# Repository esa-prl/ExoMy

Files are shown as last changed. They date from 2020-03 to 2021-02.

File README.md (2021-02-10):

# ExoMy - Documentation Repository
This repository contains all the files of the documentation of ExoMy. Click on [*Releases*](https://github.com/esa-prl/ExoMy/releases) and download the files of the latest release.
The release file contains the 3D files (STL, SLDPRT & STEP), circuit diagrams, part lists, etc. to build your own ExoMy.
The building process and the files are explained further in the [wiki](https://github.com/esa-prl/ExoMy/wiki).

# ExoMy Project Structure
Overview of other parts of the ExoMy project.

### [Wiki](https://github.com/esa-prl/ExoMy/wiki)
The [wiki](https://github.com/esa-prl/ExoMy/wiki) contains step by step instructions on how the 3D-printed rover ExoMy can be built, controlled and customized.  

<!-- ### [Documentation Repository](https://github.com/esa-prl/ExoMy)
This repository contains all the files of the documentation of ExoMy. Just click on [*Releases*](https://github.com/esa-prl/ExoMy/releases) and download the files of the latest release. They are explained further in the [wiki](https://github.com/esa-prl/ExoMy/wiki). -->

### [Website](https://esa-prl.github.io/ExoMy/)
There is a website about ExoMy. It does not help you build it, but is still nice to look at.

### [Software Repository](https://github.com/esa-prl/ExoMy_Software)
This repository contains the software to run Exomy. The [wiki](https://github.com/esa-prl/ExoMy/wiki) explains you how to use it.

### Social Media
<!-- Add icon library -->
<link rel="stylesheet" href="https://use.fontawesome.com/releases/v5.13.1/css/all.css">

<!-- Add font awesome icons -->
<p>
    
    <a href="https://discord.gg/gZk62gg"> Join the Community!</a>  
</p>
<p>
    
    <a href="https://twitter.com/exomy_rover"> @ExoMy_Rover</a> 
</p>
<p>
    
    <a href="https://www.instagram.com/exomy_rover/"> @ExoMy_Rover</a>
</p>

ExoMy image

### Publications

If you use this work in an academic context, please cite the following publication:

* M. Voellmy and M. Ehrhardt: **ExoMy: A Low Cost 3D Printed Rover**. International Symposium on Artificial Intelligence, Robotics and Automation in Space (i-SAIRAS), 2020. ([PDF](https://www.researchgate.net/publication/344874558_ExoMy_A_Low_Cost_3D_Printed_Rover))

        @inproceedings{inproceedings,
        author = {Voellmy, Miro and Ehrhardt, Maximilian},
        year = {2020},
        month = {10},
        pages = {},
        title = {ExoMy: A Low Cost 3D Printed Rover}
        }

### Acknowledgements

ExoMy was developed in the Planetary Robotics Laboratory of the European Space Agency.

The current team developing and maintaining ExoMy consists of Maximilian Ehrhardt, Miro Voellmy and Lorenzo Cervantes.

ExoMy Generations

We thank Shanker Ganesh Krishanmoorthy and Levin Gerdes for the development of the initial prototype, David Honess and Elsa María Sánchez for participating in the documented assembly, Tim Wiese and Mattia Haas for their inputs and contributions to the mechanical design, and finally Martin Azkarate, Martin Zwick and Gianfranco Visentin for enabling and continuously supporting the project.

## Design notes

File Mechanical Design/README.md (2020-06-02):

# CAD Design Guidelines

ExoMy was designed using SolidWorks 2018. No additional toolboxes were used.

## Folder Structure
Assemblies and 3D printed parts are to be stored in the main folder.

```
- Mechanical Design
Assemblies and parts go here.
-- Cables
-- Drawings
-- Fasteners
-- Purchased Parts
-- Templates
```

## Part Naming
The file naming convention is as follows:

**Assemblies**

*`Axx_Name_with_underscore.SLDASM`*

**3D-Printed Parts**

*`Pxx_Name_with_underscores.SLDPRT`*

Replace xx with a new two-digit part-/assemby-number.

**Always** use a new number for a new part/assembly. Don't try to fill in the gaps that occur if old parts are deleted.

## Configurations
Configurations are used to generate variations of parts (rear/side bogie, left/right wheelbracket, various hats.). They are also used to create drawings and bill of materials. All *`AI_*`* & *`MI_*`* drawings are linked to a similarly named configuration of the main assembly or a subassembly. This allows the generation of a bill of materials, which can then be exported to Excel.

The naming should be kept consist to simplify the referencing in the wiki in case of new releases.

## Exporting and Releases
Refer to the [wikipage](https://github.com/esa-prl/ExoMy/wiki/Release-Procedure#solidworks).

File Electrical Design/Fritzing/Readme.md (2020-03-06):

# ExoMy Fritzing project

This folder contains everything you need to open the ExoMy electronics as a Fritzing project.

## Exomy.fzz
Is the main Project file.

## Exomy_bin.fzbz
The library file that contains all the parts used for the project.

## parts
All the Fritzing pars used in the project. The files are normal archives and can be opened with any archive program, to access the underlying svg files.
## exports
The exported views of breadboard and schematic as pdf and svg file format.

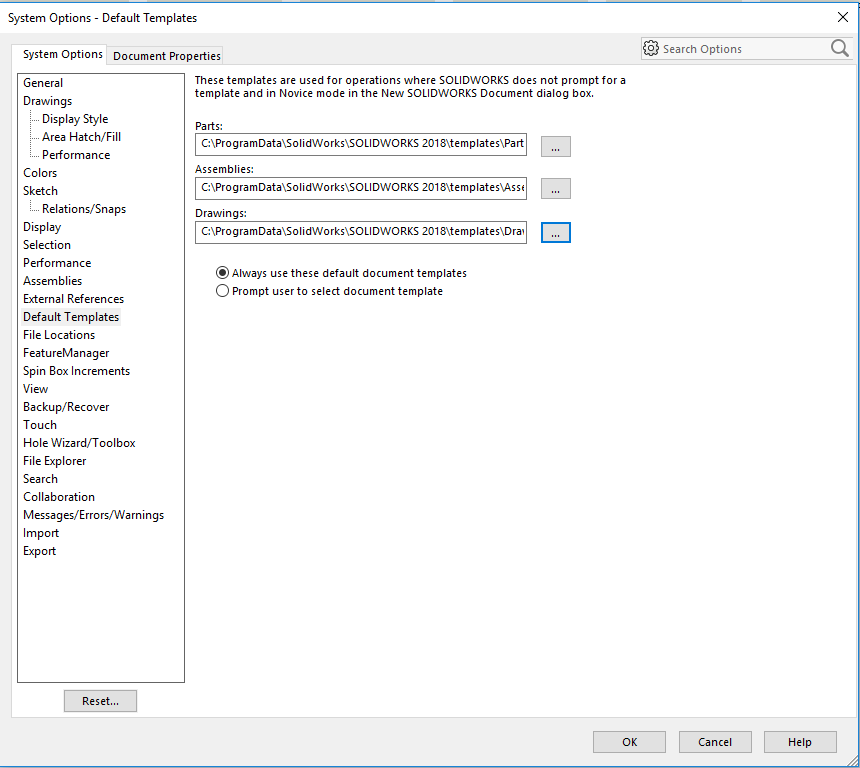
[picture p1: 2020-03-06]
Mechanical Design/Templates/CopyTemplateToDefaultLocationAndChangeDefaultTemplate.PNG

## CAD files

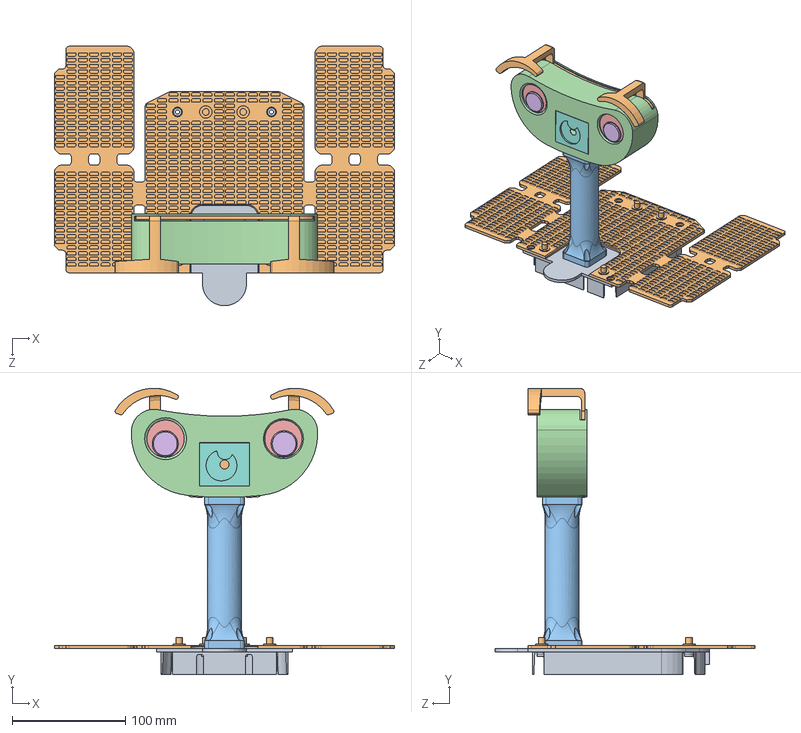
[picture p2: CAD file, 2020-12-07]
Mechanical Design/A08_Top_Assembly.SLDASM
300.0 x 252.8 x 229.0 mm
P11_Top
P12_Solar_Panel x 2
P21_Mast
P20_Head
P22_Eye_White x 2
P23_Eye_Pupil x 2
P24_Mouth_Latch
P25_Mouth
P33_Cam_Holder_Flat
P26_Hat

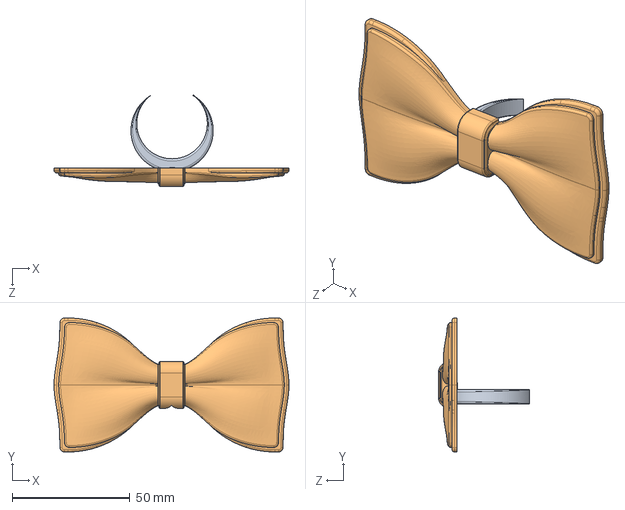
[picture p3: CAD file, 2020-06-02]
Mechanical Design/Optional Parts/A07_Neck_Decoration.SLDASM
100.0 x 57.0 x 38.9 mm
P35_Neck_Clip
P36_Bow_Tie

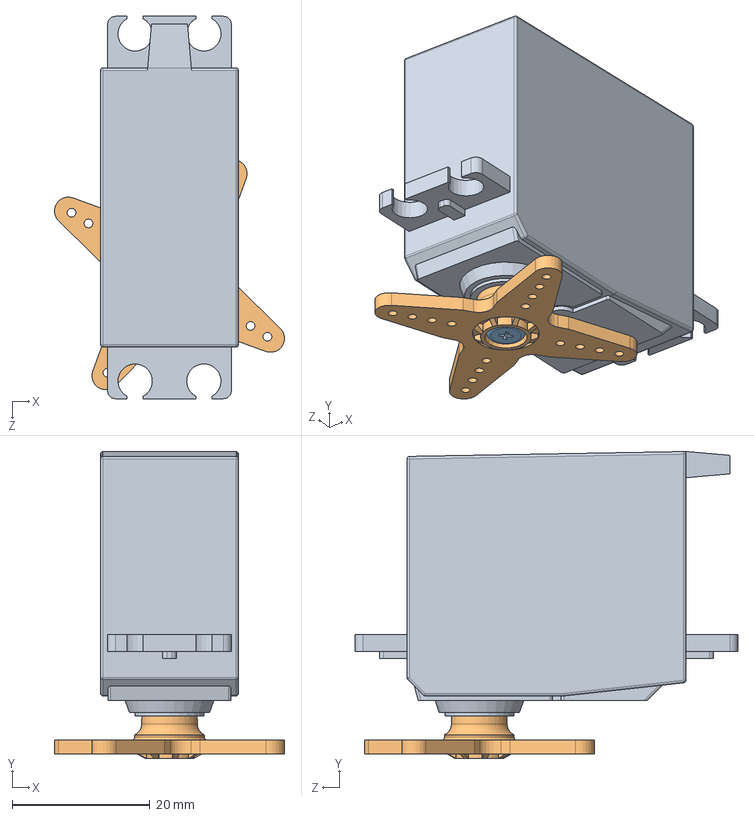
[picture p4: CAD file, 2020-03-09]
Mechanical Design/Purchased Parts/Parallax-Servo-ASM.SLDASM
33.5 x 44.7 x 55.6 mm
Parallax-Servo
Parallax-Servo-Horn
Parallax-Servo-Screw

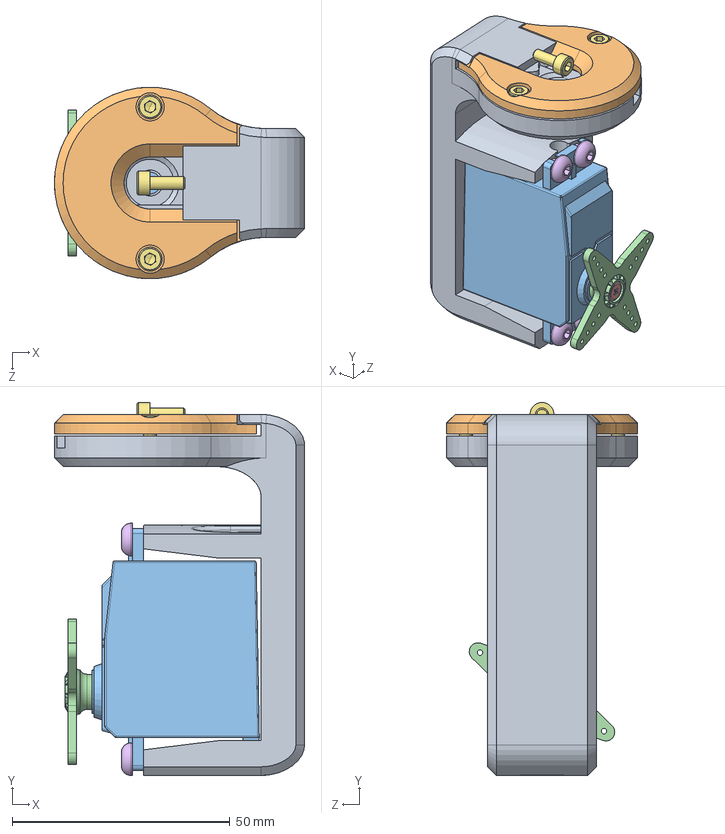
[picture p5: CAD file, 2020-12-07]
Mechanical Design/A04_Wheel_Assembly.SLDASM
57.5 x 85.7 x 44.0 mm
P28_Wheel_Bracket_Split
P29_Wheel_Bracket_Fixing_Plate
Parallax-Servo
Parallax-Servo-Horn
Parallax-Servo-Screw
CSHBTS-SUS-M4-10 x 4
SCB3_8 x 4

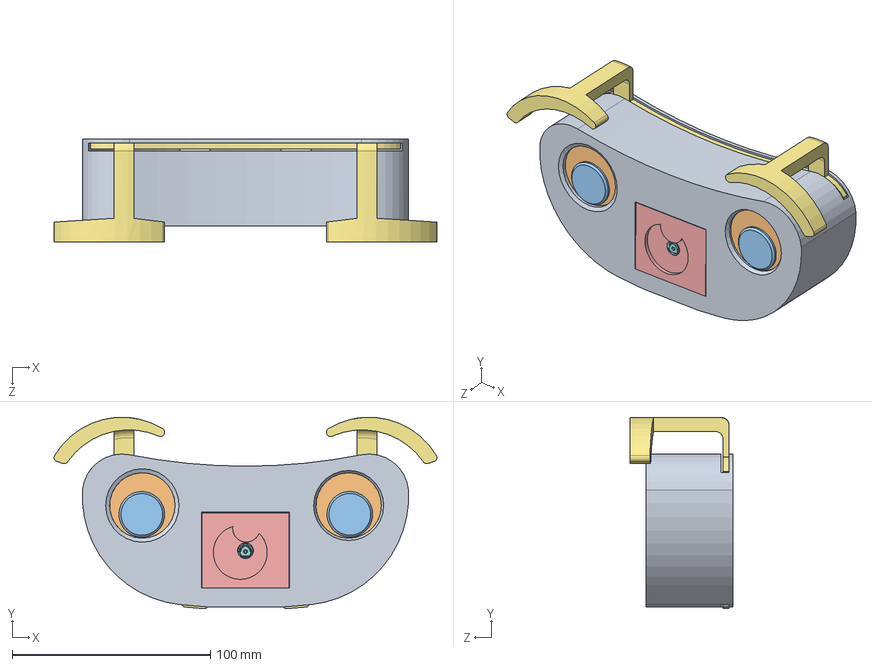
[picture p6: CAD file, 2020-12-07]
Mechanical Design/A06_Head.SLDASM
193.1 x 96.5 x 52.0 mm
P20_Head
P22_Eye_White x 2
P23_Eye_Pupil x 2
P24_Mouth_Latch
P25_Mouth
P33_Cam_Holder_Flat
P26_Hat
Raspberry Pi Camera V2
SFB3_6 x 8
SCB2_5 x 4
SCB3_8 x 2

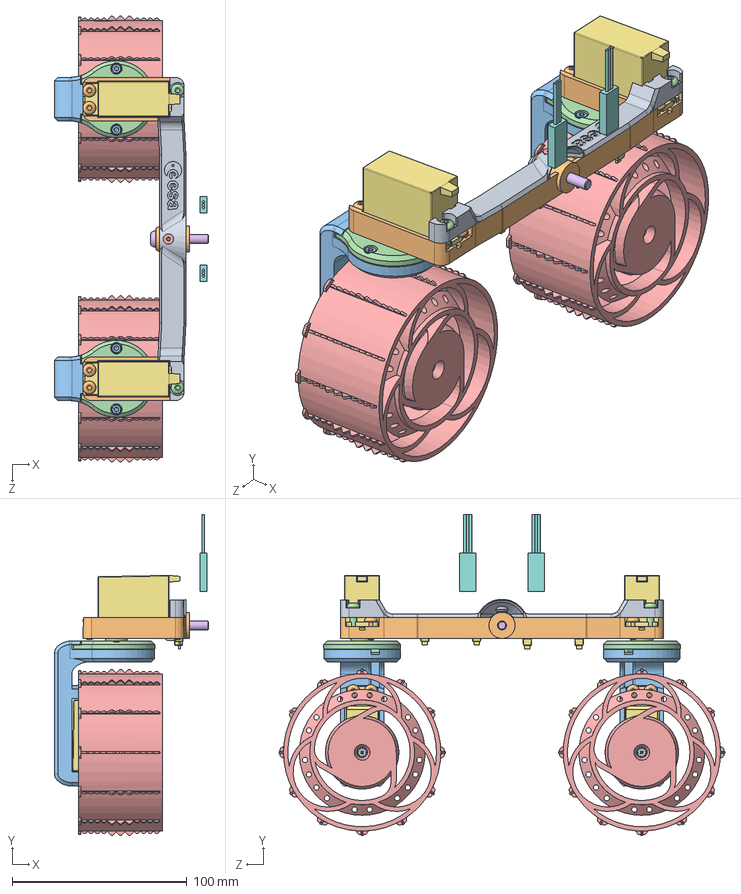
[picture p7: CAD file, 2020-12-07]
Mechanical Design/A05_Bogie.SLDASM
88.3 x 183.7 x 255.2 mm
P17_Bogie_Cable_Cover
P19_Bogie
P28_Wheel_Bracket_Split x 2
P29_Wheel_Bracket_Fixing_Plate x 2
P30_Wheel x 2
P32_Wheel_Fixing_Plate_U_Shape x 2
Parallax-Servo x 4
Parallax-Servo-Horn x 4
Parallax-Servo-Screw x 4
CSHBTS-SUS-M4-10 x 14
SCB3_8 x 8
CSHBTS-SUS-M4-16 x 2
SFB3_6
CSHBTS-SUS-M5-30
Zip_Tie x 4
Servo Extension Cable x 2

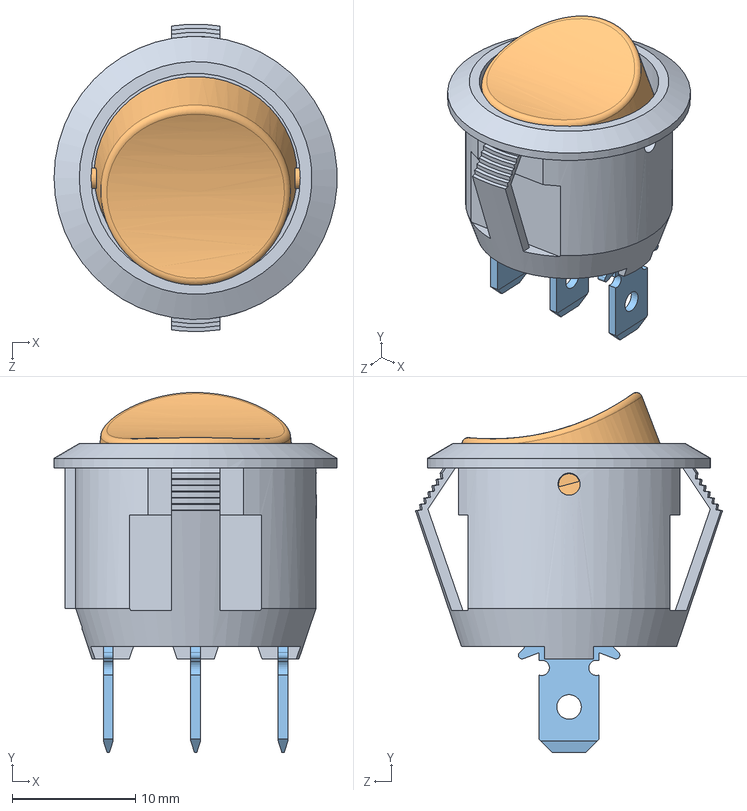
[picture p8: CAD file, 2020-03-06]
Mechanical Design/Purchased Parts/Rocker Switch.SLDASM
23.0 x 29.2 x 25.0 mm
Arcolectric Rocker Switch Housing.stp
Arcolectric Rocker Switch Rocker.stp
Arcolectric Rocker Switch Contact.stp x 3

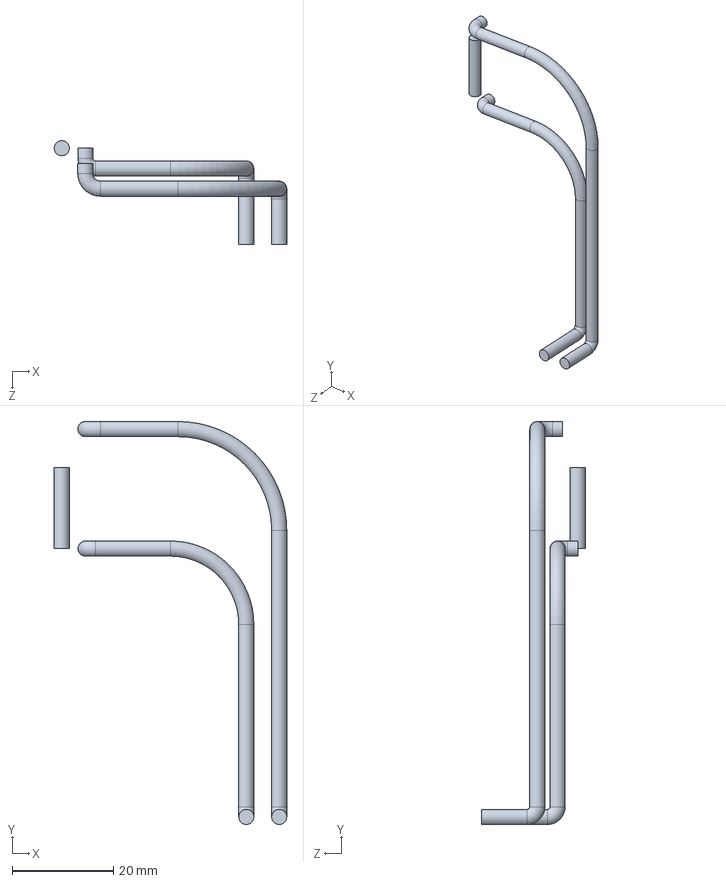
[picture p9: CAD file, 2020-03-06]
Mechanical Design/Cables/Switches_to_DCDC_Cable.SLDPRT
45.9 x 79.6 x 20.5 mm

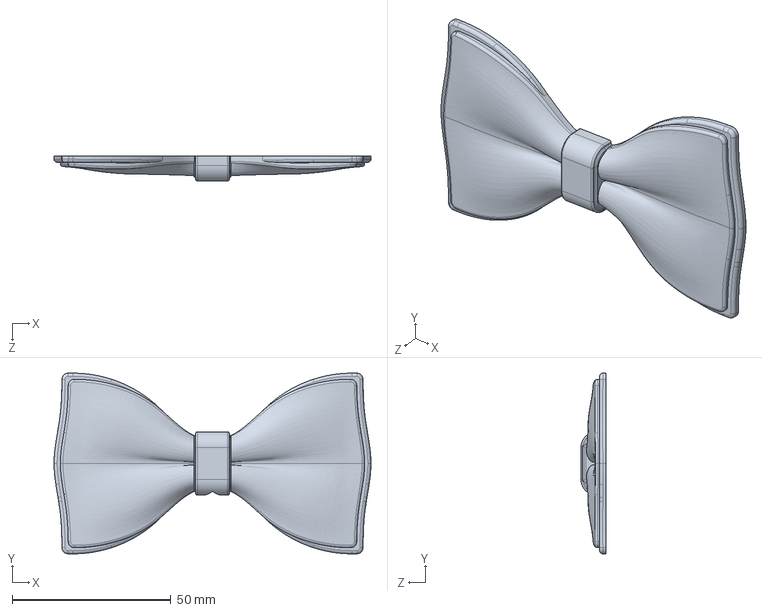
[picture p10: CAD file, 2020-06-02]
Mechanical Design/Optional Parts/P36_Bow_Tie.SLDPRT
100.0 x 57.0 x 7.87 mm

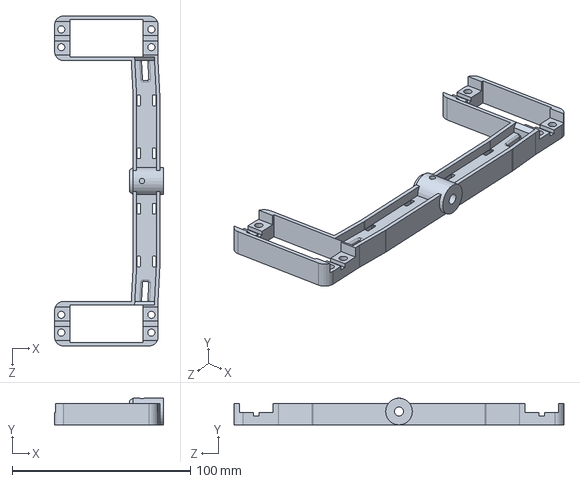
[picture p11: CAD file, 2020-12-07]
Mechanical Design/P19_Bogie.SLDPRT
61.0 x 15.0 x 185.0 mm

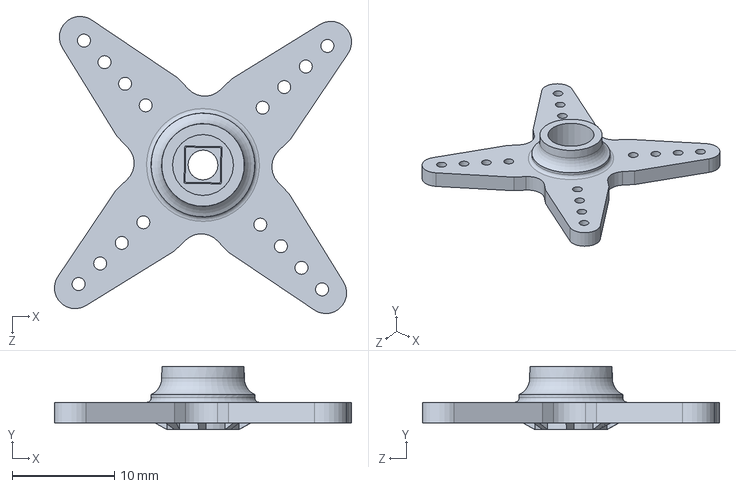
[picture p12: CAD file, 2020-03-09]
Mechanical Design/Purchased Parts/Parallax-Servo-Horn.SLDPRT
29.1 x 6.17 x 29.1 mm

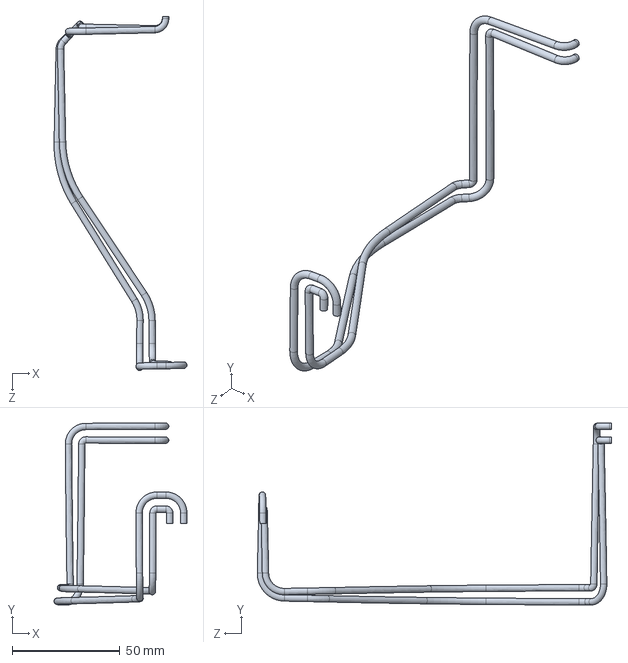
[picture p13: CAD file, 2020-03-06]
Mechanical Design/Cables/Battery_to_Switch_Cable.SLDPRT
61.7 x 84.5 x 164.5 mm

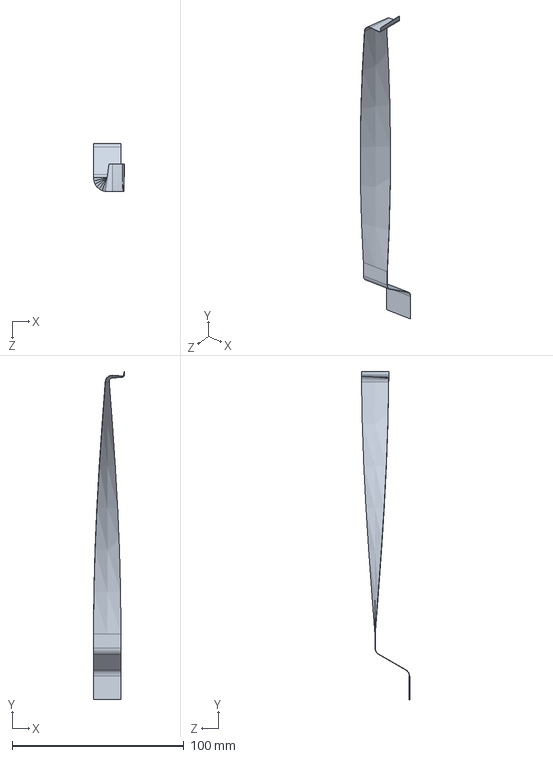
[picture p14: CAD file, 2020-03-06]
Mechanical Design/Cables/Long_Camera_Cabel.SLDPRT
18.1 x 191.0 x 28.1 mm

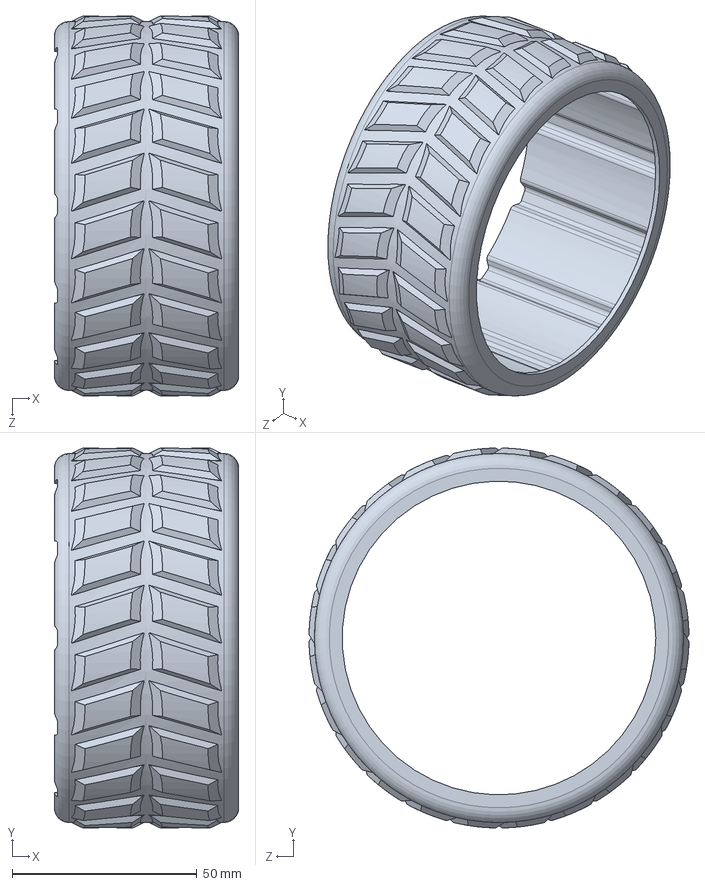
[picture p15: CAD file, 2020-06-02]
Mechanical Design/Optional Parts/P37_Wheel_Sleeve.SLDPRT
50.0 x 103.0 x 103.0 mm

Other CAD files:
Mechanical Design/P28_Wheel_Bracket_Split.SLDPRT
Mechanical Design/Purchased Parts/XT-60_Macho Male Pins.SLDPRT
Mechanical Design/Cables/USB-C Plug.SLDPRT
Mechanical Design/Optional Parts/P34_Hat_Rack.SLDPRT
Mechanical Design/Cables/DCDC_to_PWM_Board_Cable.SLDPRT
Mechanical Design/Cables/Power_Switch_to_DCDC_Cable.SLDPRT
Mechanical Design/Cables/Servo Extension Cable.SLDPRT
Mechanical Design/Drawings/AI_Chassis_BoM.SLDDRW
Mechanical Design/Drawings/AI_Head_BoM.SLDDRW
Mechanical Design/Drawings/AI_Rear_Bogie_BoM.SLDDRW
Mechanical Design/Drawings/AI_Side_Bogie_BoM.SLDDRW
Mechanical Design/Drawings/AI_Top_BoM.SLDDRW
Mechanical Design/Drawings/MI_Printed_Parts_BoM.SLDDRW
Mechanical Design/Drawings/MI_Wire_Harness_BoM.SLDDRW
Mechanical Design/Fasteners/Button Head/CSHBTS-SUS-M3-10.SLDPRT
Mechanical Design/Fasteners/Button Head/CSHBTS-SUS-M4-10.SLDPRT
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

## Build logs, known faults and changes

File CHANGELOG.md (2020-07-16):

# Changelog

## [v1.0.2] - 2020-07-16
- add "Optional Parts" containing various add-ons.
	- Flexi fill indoors tires
	- Bowtie
	- Universal neck decoration mount
- fix URL in purchasing BoM of M4x16 button head screw
- increase height of P15_DCDC_Holddown.SLDPRT and standoffheight of P01_Chassis.SLDPRT to match screw length correctly.
- add chamfers to holes in P20_Head.SLDPRT.
- add SolidWorks view-cameras to A01_ExoMy.SLDASM

## [v1.0.0] - 2020-03-09
- first released version of ExoMy

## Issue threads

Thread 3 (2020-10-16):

Number of required servos is unclear (16 or 12?)

MartinSpiessl, 2020-10-16:
Thanks for making this project open source/open hardware!

I have a small question regarding the required components.
The BOM states that we need the following:

```
6 | Parallax-Servo | Steering Modded
10 | Parallax-Servo | Continuous
```

But from the building instructions I could only find that 6 of each (= 12 servos total) are used in the bogie.
What is the intended use for the other servos?
Where these simply left on the BOM, e.g. because you originally planned to make the head orientable?

mvoellmy, 2020-10-17:
You're welcome :) You are right, ExoMy only needs 12 motors (6 for steering and 6 for driving).
In which BoM did you find that 10 coninuous servos are needed? In the .xlsx and the .pdf it mentions correctly 6 each:
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

mvoellmy, 2020-10-17:
Also we would be happy if you join our discord server and to share your progress :)

https://discord.gg/gZk62gg

MartinSpiessl, 2020-10-20:
I know see what happened. I had the collapsed version of BOM so I didn't realize the first column are actually increasing IDs but misinterpreted them as part counts.

Thanks for the clarification!

> Also we would be happy if you join our discord server and to share your progress :)

Thank you, maybe in time I will. I have not yet started, I was just trying to get an overview of the involved components.

Closed 2020-10-20.

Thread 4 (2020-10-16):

BOM xlsx file contains hidden rows which might be overlooked by people

MartinSpiessl, 2020-10-16:
When I open https://github.com/esa-prl/ExoMy/wiki/v1.0.2/BoM/PI_ExoMy_Purchasing_BoM.xlsx in libreoffice, some of the rows are not displayed by default.

This can be confusing to people, as they might not be aware that the file also contains detailed information about the other parts as well.

They might then try to figure out the details from https://github.com/esa-prl/ExoMy/wiki/v1.0.2/Technical_Drawings/PDF/PI_ExoMy_All_Parts_BoM.pdf which will lead to frustration, since the information there is not detailed enough for actually purchasing the parts.

mvoellmy, 2020-10-17:
Good find! The rows are hidden due to a filter that was commited and pushed accidentally. I updated the file and it should now show all parts again by default.

Closed 2020-10-17.

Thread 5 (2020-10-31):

some website wiki improvement suggestions

pebe-espana, 2020-10-31:
links to "wiki" do not lead to explanation wiki - see annotated screenshot
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

pebe-espana, 2020-10-31:
Now same "problem" permeates the site - what is needed is that references to wiki should point to a page (like content page) of the links on the right hand side bulleted list. Repeatedly ran into just wanting to look up some point and clicking on wiki or title of a para that lead to the same page. so extra content table page could help?

pebe-espana, 2020-10-31:
In the instructions for Bogie assembly, maybe a diagram as attached could be helpful to indicate the 180 degree swing range wanted? Although photos are helpful, it is easy to get all confused what the end result should be. (In fact, I hope I got it right ;-) )
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

maxehrhardt, 2020-11-09:
The wiki README has been updated with more useful links and text. The instruction schematic for the bogies is in the making.

mvoellmy, 2020-11-09:
Added a schematic indicating the desired range of motion. Thanks for the inputs @pebe-espana!

Closed 2020-11-09.

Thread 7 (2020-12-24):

Minor typo

j-dohnalek, 2020-12-24:
**Problem:**

https://github.com/esa-prl/ExoMy/wiki/Bogie-Assembly#install-steering-motors

the  bill of materials does not say M4x12 it only says M4x10

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

**Solution:**

Change the instructions to M4x10

mvoellmy, 2020-12-25:
Thanks! Fixed it.

Closed 2020-12-25.

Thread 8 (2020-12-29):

Error in P03_BogieBearing

berendj, 2020-12-29:
The four holes in the corners of this part have a bore of 4mm, while they are supposed to hold a 4mm bolt. The diameter of these holes should be 3.3mm

mvoellmy, 2020-12-29:
While 3.3 mm is the right core hole for threading an M4, it would be too small here.
First, we recommend to "cut" the threads directly with the screws and don't use a thread-cutters. Screwing in a screw in a 3.3 mm whole would require too much force from our experience.
Second, a 4 mm hole in CAD will be much smaller in the print. Maybe around 3.7-.8 mm (never measured it). We found 4 mm to work well in terms of rigidity, reliability and ease of installation, so it should stay 4 mm.

berendj, 2020-12-29:
Hello  Miro Voellmy,

Your first point is well taken, 3.3mm is for threading an M4. But I changed the design to 3.4mm and just did the threading with an M4 bolt without problems, but needed some force indeed.You wrote “Second, a 4 mm hole in CAD will be much smaller in the print. Maybe around 3.7-.8 mm (never measured it).”

As we say in Dutch “Meten is weten” as you may well know. A CAD designed 4mm hole IS 4mm, unless you never calibrated your 3D-printer.

I did and a 4mm bolt can be pushed through without force, apart from a little “elephant foot” at the bottom of the print.

I would appreciate you add a comment to the closed issue #8 to make others aware your choice and the consequence if they have calibrated their printer.

met vriendelijke groeten,

Bert Ruiterkamp

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

mvoellmy, 2021-01-06:
Fair point regarding calibration. I assume you tuned your slicer using the Horizontal Expension parameter?
https://bradshacks.com/3d-printing-tolerancing/
I was not aware of this parameter and with that in mind I have to agree, that a smaller hole size would have been better.

I updated the wiki, adding a recommendation that people test the threads before printing all the parts.
https://github.com/esa-prl/ExoMy/wiki/3D-Printing

I will reopen the issue, but can not change it myself. As I'm not working at ESA anymore, I don't have access to Solidworks anymore nor the 3D printers (which should be calibrated ;) to test the fit. It would be good to change this in the future however.

berendj, 2021-01-06:
Actually Cura has an even better feature. Horizontal Expansion enlarges or minimizes also the basic print size of your object. Cura has (in expert and all modes) a feature called Hole Horizontal Expansion. That leaves the overall object size unchanged and affects only the hole radius. See [this video](https://www.youtube.com/watch?v=UUelLZvDelU) for an explanation.

I had to reprint the bogies because the bolts for the servo's did not hold. I also hope the mast will hold on the chassis top. These holes also seem a bit wide.

Penguin-fach, 2021-01-13:
Getting threads to hold reliably in PLA over time is problematic particularly with shock loading if you are going to drive over obstacles. I have found brass knurl nuts very easy to fit with a soldering iron and make an enormous difference to thread performance in all 3D printed parts. Has anyone tried this on ExoMy as yet?

Regards, Frazer

mvoellmy, 2021-01-13:
Hey @Penguin-fach,
Agreed, brass inserts are amazing. I'm a big fan of them myself and an ExoMy with full brass inserts would definitely be great.

Currently we use brass inserts to fix the top to chassis. This is a part that we expect to be removed somewhat regularly. Thus the reusability you gain with the brass inserts should pay off.

On the other parts, we stuck with the direct cutting method to keep the complexity and assembly time of ExoMy low. So far we had threads which were too loose, but no failures in the threads occurred during operation.

We received an email of someone who wants to modify the STEP files of ExoMy to work with brass inserts, but I don't know what their current progress is.

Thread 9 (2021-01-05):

American Providers BOM

durinwinter, 2021-01-05:
We have sourced everything from Sparkfun and some of the parts change, am curious if we can upstream wiki/BOM changes once we have everything resolved.

mvoellmy, 2021-01-06:
Hey @durinwinter! That sounds like a good idea.
I suggest to add a second column to `PI_ExoMy_Purchasing_BoM.xlsx` containing the US suppliers.
Once it's finalized, please attach it here and I can update it in the release and make sure the link in the wiki points to the new one.

maxehrhardt, 2021-03-01:
@durinwinter Is there any update on the BOM?

durinwinter, 2021-03-01:
yes! I have it - one thing I am missing is the dcdc 11.5v to 5v. but
besides that I have it.
<https://www.winterwinds.io/>
Caleb Eastman

Co-Founder, C3PO
M:  970.632.1890
P:  303.551.0570
E:  caleb@winterwinds.io
A: 1910 Pike Rd Unit A, Longmont, CO 80501
www.winterwinds.io
<https://www.linkedin.com/in/caleb-eastman-55465352/>
<https://twitter.com/winterwindsr>
<https://www.instagram.com/winterwindsrobotics/>
<https://www.facebook.com/winterwindsrobotics/>
<https://mysignature.io/editor/?utm_source=expiredpixel>

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

durinwinter, 2021-03-01:
[ExoMy_Purchasing_BoM.xlsx](https://github.com/esa-prl/ExoMy/files/6064703/ExoMy_Purchasing_BoM.xlsx)

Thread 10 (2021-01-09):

Incomplete sentence in the wiki

jcranky, 2021-01-09:
Hi :)

I just started reading the wiki, to learn a bit more about how to put this together. There is a sentence that seems to be cut, here:

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

Allows what?
Not a big deal, of course.

maxehrhardt, 2021-01-10:
Thanks for pointing this out. Looks not so good, especially on the first page.
I fixed it!

Closed 2021-01-10.

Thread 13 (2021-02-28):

Wrong Docker startup code in wiki

0xD0M1M0, 2021-02-28:
On the page "Final Integration" the docker startup for the motor config says:

sh ~/ExoMy_Software/docker/run_container.sh -c

Correct would be:
sh ~/ExoMy_Software/docker/run_exomy.sh -c

maxehrhardt, 2021-03-01:
Thanks for finding, is fixed now.

Closed 2021-03-01.

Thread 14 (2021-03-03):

Cable protection required

0xD0M1M0, 2021-03-03:
During driving the rover the cable tend to get caught in the wheels or rub against the "P03_Bogie_Bearing_Default". In my case I saw after a few hours of test driving serious cable wear.

I used following solutions combinations to protect or mitigate the risk of cable wear:
- all cables are wrapped longitunal carefully in electrical tape on exposed areas until they are inside the housing. Exposed areas are: inside the "P28_Wheel_Bracket" (specifically on the top turn), after leaving the "P28_Wheel_Bracket" until passing the first zip tie inside the "P19_Bogie" and passing through the "P03_Bogie_Bearing"
- used the unconventional rubber band solution to tie the cables into an upward direction between "P28_Wheel_Bracket" and "P19_Bogie". In the rear the rubber band goes to the outer zip tie position around the bogie, in the front upwards around the motor and in the center also around the motor
- in the center, I exited the cable on the top of the "P28_Wheel_Bracket" by removing on each side of "P29_Wheel_Bracket_Fixing_Plate_Default" one end that slides under the "P28_Wheel_Bracket" allowing for enough space to exit the cables. Afterwards I was able to pull up the cable with the rubber band.

One open spot for the cables are the "exits" outside the "P28_Wheel_Bracket". Currently I use shrink tubes that are cut open and then clamped into the whole setup. But they tend to fall out.

Maybe these topics can be addressed in the wiki in the appropriate chapters. This would allow a longer lasting experience while driving the rover.

maxehrhardt, 2021-03-03:
Great work! I will have a look on how to add those information to the wiki.
Can you provide some explaining pictures for the parts that needed to be fixed?
It is mostly easier to show stuff, then to explain.

0xD0M1M0, 2021-03-03:
Here are some pictures. You will notice, that instead of opening the motors for cable routing, I added golden motor covers. This saved me some trouble. Currently, the rear bogie has no electrical tape as it the cables never went close to the wheel due to the rubber bands. The electrical tape makes the cables quite stiff. Therefore I tried once to also tape the "exits" from "P28_Wheel_Bracket", but that didn't go to well as the cable was bend not nicely, risking a cable break from the inside.

I currently have the bogie covers on so, sadly no quick pictures of the protected cables through the "P03_Bogie_Bearing".

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
-> Shows the two different modes for "P29_Wheel_Bracket_Fixing_Plate_Default" for the center wheels.
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
-> Here you see the cable routing for the center wheels
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
-> Rear wheel assembly with rubber band alignment. Here two small dropshaped cuts in the "P19_Bogie_Rear Bogie" on both sides to fix the rubber band without my need of a zip tie would make it look even better.
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
-> Rear wheel assembly with rubber band alignment. You can see here the shrink tube coming out of the wheel assembly. But this is not perfect. I tried stretching the shrink tube to fit it over the connector, so I don't have to cut it open, but with a 2 cm long piece, it was not easy. Maybe a bigger shrink tube could help, but they are currently not part of the BoM, so I didn't have them.
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
-> Front wheel assembly with rubber band alignment.
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
-> Front wheel assembly with rubber band alignment and motor cover.

0xD0M1M0, 2021-09-07:
The wiki was updated on the following pages to address this issue:

[Purchasing Instructions](https://github.com/esa-prl/ExoMy/wiki/Purchasing-Instructions)
[Bogie Assembly](https://github.com/esa-prl/ExoMy/wiki/Bogie-Assembly)

Closed 2021-09-07.

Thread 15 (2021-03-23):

CAD drawings

edhage, 2021-03-23:
Hello, could you please save the CAD drawings in Step-format so I (and probably many others) can read it in any CAD-program? (Tried to read it in Inventor 2018 that recognises sldprt and sldasm, but the 2018 was too old).

edhage, 2021-03-23:
I see step is added in the release-file. So very good. However, an assembly would be appreciated.

mvoellmy, 2021-03-23:
Hey!
The file ```A01_ExoMy_Default.step``` is an assembly of the whole rover. It's in the same folder ```ExoMy Release/Parts/STEP```as the other step files.
Cheers
Miro

edhage, 2021-03-25:
thanks for the info

Closed 2021-03-23.

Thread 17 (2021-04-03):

pi camera image and direction control not visible in web page

juergmaier, 2021-04-03:
I have tried to locally see the web front end (keyboard, mouse, hdmi and ethernet connected to the raspi)
I enter 127.0.0.1:8000 in my browser (chromium) and see a web page.
It contains only the 3 buttons for drive type + motor enable/disable, no direction icon and no camera picture

I have tried to check on the cam and it took me a while to understand that it is usually occupied by the auto running exomy software.
That was why I received an error with raspistill -v -o mycam.jpg I assume?
Stopping the exomy service with -s option of the script and rerunning the raspistill shows me the cam's view.

What to do to get a fully working web page?

Regards
Juerg

juergmaier, 2021-04-04:
after adding the missing roslib.min.js to the exomy_ws/src/exomy/gui folder the image and joystick is showing.

Closed 2021-04-04.

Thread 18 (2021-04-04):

P02_Drill_Default: STEP File with wrong content

0xD0M1M0, 2021-04-04:
ExoMy Release v1.0.0 package:
Parts -> STEP -> P02_Drill_Default.step
STEP file does not contain the Drill Default part.

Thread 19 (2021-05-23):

3D print part in a more common format ?

romgere, 2021-05-23:
Hi, I'd like to start building an ExoMy, but I don't have access to any solidworks copy.

Any change to see the 3D part shared with a more common format ? A format allowing open source CAD software ?

I think I could be a good idea also if you want your project to be more accessible to public 😃

Thx 🙏🏻

romgere, 2021-05-23:
Juste a small update, I found a way to try solid thx to offical site...

I saved the "main" `A01_ExoMy` file to `.Step`& it seems enough to open all parts in an open source 3D software, like freecad :

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

romgere, 2021-05-23:
Of course when you don't look at the right place... Didn't see STL & STEP was available in the release 🤦🏻

Closed 2021-05-23.

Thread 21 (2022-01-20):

Funktion

GGoergen, 2022-01-20:
My ExoMy is ready, everything calibrated. Now when I turn it on I can't access the WebGui, neither does the remote control via gamepad work. Nothing moves. The Raspi can be operated via HDMI, keyboard and mouse, the ServoHat also works???

0xD0M1M0, 2022-01-21:
Hello @GGoergen,
I am happy to help. The easiest and best way is to join the Discord community (https://discord.gg/gZk62gg) for Exomy and ask the question there. There are many people happy to help and maybe makes the communication easier.

If you like to stay here, please provide the setup and how far you progressed in the assembly and startup wiki entry.

0xD0M1M0, 2022-01-26:
Solved by GGoergen:

> Tip from the ExoMy WIKI: ROS cant find files
> Try sourcing the ROS development environment again with source devel/setup.bash. This command should be executed in the exomy_ws. That's needed when a new terminal is started.

Closed 2022-01-26.

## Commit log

2020-03-06 added fritzing
    [ExoMy.fzz]
2020-03-06 release of mechanical design v1.0.0
    [A04_Wheel_Assembly.SLDASM, A05_Bogie.SLDASM, A06_Head.SLDASM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]
2020-03-09 added wheel to first release
    [A04_Wheel_Assembly.SLDASM, A05_Bogie.SLDASM, A06_Head.SLDASM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]
2020-06-02 release v1.0.1 commit
    [A04_Wheel_Assembly.SLDASM, A05_Bogie.SLDASM, A06_Head.SLDASM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]
2020-06-02 updated Changlog v1.0.1 date to current one
2020-07-16 move hat rack to optional parts
    [P34_Hat_Rack.SLDPRT]
2020-07-16 add chamfers to holes in P20_Head
    [A06_Head.SLDASM, A08_Top_Assembly.SLDASM, P20_Head.SLDPRT]
2020-07-16 update Tires and Tie tag in changelog
2020-10-05 Add additional camera and section views to assembly.
    [A06_Head.SLDASM, A08_Top_Assembly.SLDASM, P26_Hat.SLDPRT]
2020-10-28 URDF export
    Added reference geometry for the URDF export
    Created URDF export display state
    [A04_Wheel_Assembly.SLDASM, A05_Bogie.SLDASM, P03_Bogie_Bearing.SLDPRT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]
2020-11-17 Add moustache mouth
    [A04_Wheel_Assembly.SLDASM, A05_Bogie.SLDASM, A06_Head.SLDASM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]
